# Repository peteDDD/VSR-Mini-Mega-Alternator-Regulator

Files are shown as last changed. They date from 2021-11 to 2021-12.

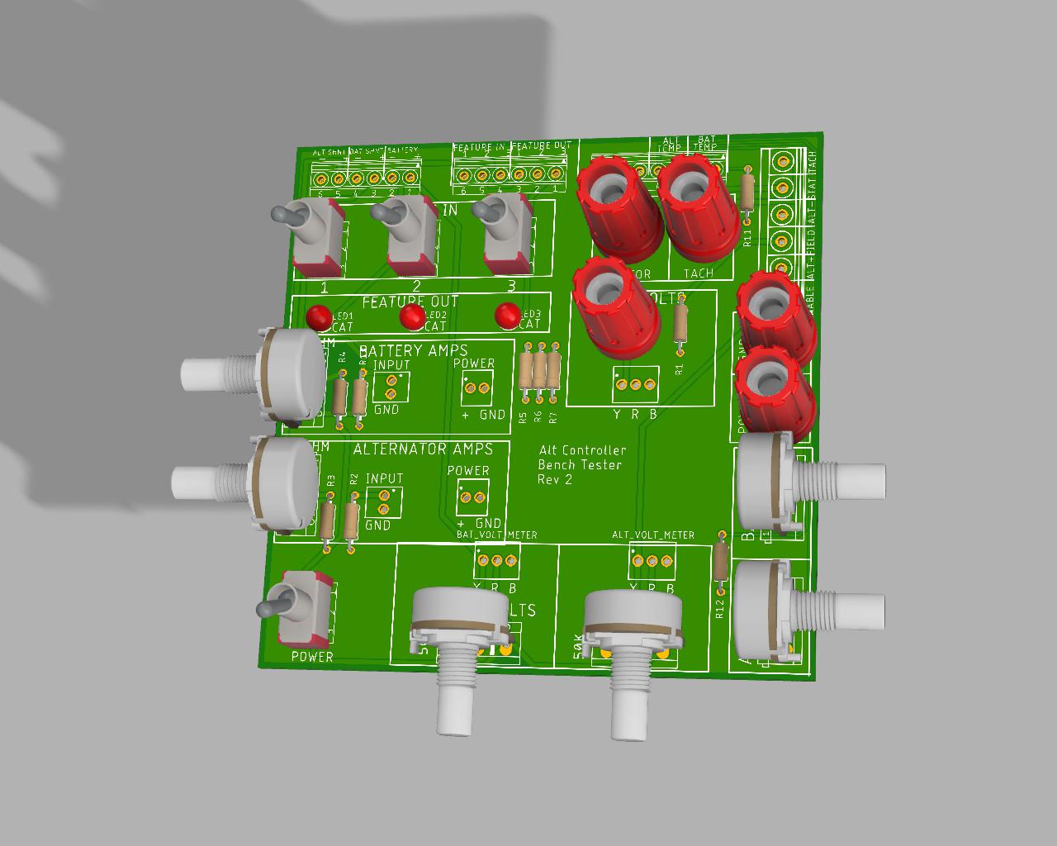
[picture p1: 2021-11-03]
Documentation/Bench Tester 0.2.jpg

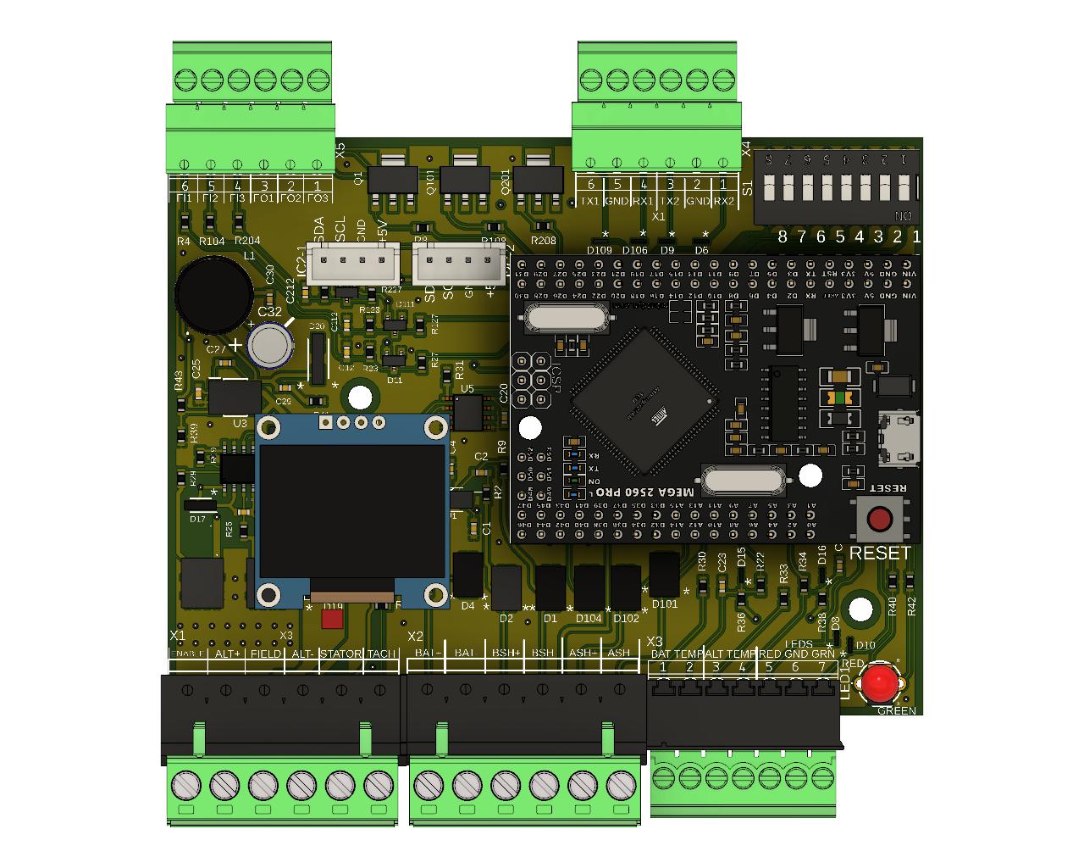
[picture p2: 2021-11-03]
Documentation/VSR Mini Mega with Connectors and oled v5.jpg

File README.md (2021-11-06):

# VSR-Mini-Mega-Rev-1

This project is a refactoring of the amazing work of William A. Thomason ("Al") to create an open source very smart alternator regulator.  That work can be seen here:
http://arduinoalternatorregulator.blogspot.com/

That open-source hardware is no longer orderable through Al.  In January 2019, that product "went pro" and is now available as a commercial product as you can see here:
http://wakespeed.com/products.html

In December 2020 I began refactoring Al's code to remove CAN and Bluetooth related code and move the hardware to a new PC board with a Mini Mega Pro 2560 daughter card
as the processor. Thus "VSR MINI MEGA" was born.

I wanted to remove some functionality and add other functionality.  Also, moving to the Mini Mega Pro 2560 provided more memory for expansion.

New hardware features include:
  - Dual INA226 current voltage sensors (for Alternator and Battery)    * Al's designs supported a second shunt but required a separate battery monitor to implement 
      that very unique and powerful functionality.  THe VSR MINI MEGA directly support two shunts.
  - Three Feature-in Ports and Three Feature-out Ports (functionality and port assignments selectable in Config.h)  
  - Two serial port screw headers, separate from port used to USB programming, one can support external full function display 
       (A remote display based on an Arduino Uno and a TFT color display will be published in the near future)
  - Two I2C pin headers to add an in-case OLED display or other features
  - Red and green LED output connections (independent of the Feature-out option which preceeded it).  
 
New firmware features include, selectable and configurable in Config.h include  :  
  - ENABLE_FEATURE_IN_SCUBA  - uses one of the Feature-in ports to shift the alternator field PWM way down so a small engine can run a SCUBA compressor while maintaining a 
      bit of output for keeping up with an electric clutch and relays used by the SCUBA compressor.
 -  FEATURE_OUT_GREEN_LED, FEATURE_OUT_RED_LED - echo the red and green status LED to your choice of Feature-out ports.
 -  FEATURE_OUT_LIFEPO_SHUTDOWN_ALARM - provides a Feature-out alarm which follows the Force-o-Float Feature-in
 -  USE_OLED - provides a class-based OLED display which displays realtime alternator and battery voltage, current, and temperatures, field PWM, current charging mode, 
      time in that mode, flags like "Forced Float" and "SCUBA", and error messages.  The display also reflects the DIP switch settings in human-speak at boot up.
 -  USE_SERIAL_DISPLAY - supports Arduio Uno-based color TFT display which alternately displays a screen showing alternator amps and battery voltage and a graphical display
      of the actual charging curve (amps and volts) over time
      
Features and firmware removed include (as best I can so far)
 -  CAN support
 -  Bluetooth artifacts from earlier VSR versions
 -  Engine control artifacts from Al's 6HP 12V diesel genset/water maker which preceded the VSR alternator regulator.
 -  Remote battery monitor artifacts
 
Future (near-term) enhancements planned:
 -  There is a stub in this release to support monitoring LiFePO4 battery management system's output for a pending battery disconnect.  This will then trigger a "Force-to-float"
      on the Mini-Mega to protect the alternator from a battery disconnect.
      
Also developed:
 -  Bench testing board to mimic battery and alternator voltages, currents, and temperatures, and feature-in and feature-out functions (switches and LEDs respectively)  
      This board also can have small volt and current meters on it and bannana jacks for stator input (from a signal generator) and tach out (to a frequency counter or 
      oscilloscope.
 -  The previously-mentioned remote color graphical display
 -  3D-printed case for VSR Mega-Mini with 0.93" OLED
 -  3D-printed bezel for the remote color graphical display

 FULL REFERENCE MANUAL CAN BE FOUND IN THE DOCUMENTATION DIRECTORY.
 
 ###

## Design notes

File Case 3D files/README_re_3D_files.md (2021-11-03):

Regarding the case lids and the OLED snap-in mount, I have found that there is some variance in the dimensions of the OLED boards.
To accomodate this, I made the snap clips a bit bigger than might be necessary.  Carefully trim *two* of the clips (I like to trim
the ones closest to the side of the case) slightly with a razor blad to adjust the degree of pressure needed to press your OLED board 
into position.

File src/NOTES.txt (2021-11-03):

started with SmartRegulatorv1.3.1.2020_12StableE_for_10b

1) DONE --  I2c.write(INA226_EXTERNAL_I2C_ADDR, CONFIG_REG, ptr, 2);  

  //DUBLER 061720    adding external INA226
  #ifdef USE_EXTERNAL_INA226
  i2c_start(INA226_EXTERNAL_I2C_ADDR << 1 | I2C_WRITE);
  i2c_write(CONFIG_REG); // Writing the Config reg also 'triggers' a INA226 sample cycle.
  i2c_write(highByte(INA226_CONFIG));// MSB always goes 1st
  i2c_write( lowByte(INA226_CONFIG));
  i2c_stop();

2) DONE -- cpu is AVR  eliminateed #ifdef AVR

3) DONE -- Change INA226 to INA226-bat  and external_INA226 to INA226-alt

4) DONE -- Scrub smartregulator.h to configure to ATmega2560 MINI PRO EMBED

5) DONE -- do we need CHARGE_PUMP_PORT (likely just for bluetooth)
   system.cpp line 424

6) DONE -- what is RVCMessages.h  used in system.h  ... NMEA2000 stuff
   GET RID OF N2K stuff

7) DONE -- research WDT on ATmega2650

8) DONE -- systemVoltMult in main code.   decide if we need this or not.

9) DONE --decide what functions we want to map to the dip switch.   Set this up in the main code.
   Perhaps add label on board for DIP switch functions  Add tach mode and engine stop function (activate feature_out_3 pulse after X time in float mode)

10) DONE -- review DIP switch code.  May be able to ifdef in simpler code since pins are now assigned to a single port.

11) DONE -- Look into #ifdef NTC_FET_PORT (not turned on yet... Pin 7 of Mega board)

12) DONE -- Change feature_out_port to support multiple feature out ports -- continue to complete... now has 
      feature in/out port defines.

13) DONE -- Move serial port for serial display out to a different serial port.  Reserve primary serial port for
    programming and configuring.  CONFIGURE MULTIPLE SERIAL STREAMS

14) On 3D printed case, engrave terminal names.

15) DONE -- have we eliminated all references to AVR and OSE_ALTERNATOR defines?

16/ DONE -- NOTE BOM R1 and R101 are now 10 ohm

17) DONE --Need to implement a failsafe for lithium batteries in the combiner funtion.

18) Confirm that Lifeline profile agrees with Lifeline specs.

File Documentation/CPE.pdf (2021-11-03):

const tCPS PROGMEM defaultCPS[MAX_CPES] = {

// eliminated decimal places to fix conversion narrowing problem. Note that, for example, 6 hours uses 60 here and 4.5 hours uses 45 | Min | Bat | Bat
// Name | BULK/ACCEPTANCE | Min | Temp Min | Max
Target | | | Limit Exit | Exit | Limit | Exit | | | | Equal Limit | Exit | Exit | Temp | Temp Chrg Chrg
Volts | Duration | Amps | Amps Volts | Duration | Volts Amps | Duration | Amps Ahrs Volts | Duration | Volts Ahrs | Volts Amps | Duration | Amps | Comp | Limit Temp Temp
{"LIFELINE" | 14.3 | 60 * 360000UL 15 | 0 | 0 | 0 * 360000UL | 13.3 | -1 | 0 * 360000UL | -10 | 0 | 12.8 | 0 * 360000UL | 0 | 0 | 0 | 0 | 0 * 360000UL | 0 | 0.0234 | -9 | -45 | 45} // LIFELINE BATTERY #1 Default (safe) profile & AGM #1 (Low Voltage AGM).
{"STD FLA" | 14.8 | 30 * 360000UL | 5 | 0 | 0 | 0 * 360000UL | 13.5 | -1 | 0 * 360000UL | -10 | 0 | 12.8 | 0 * 360000UL | 0 | 0 | 0 | 0 | 0 * 360000UL | 0 | 0.005 * 6 | -9 | -45 | 45} // #2 Standard FLA (e.g. Starter Battery small storage)
{"HD FLA" | 14.6 | 45 * 360000UL | 5 | 0 | 0 | 0 * 360000UL | 13.2 | -1 | 0 * 360000UL | -10 | 0 | 12.8 | 0 * 360000UL | 0 | 0 | 15.3 | 25 | 30 * 360000UL | 0 | 0.005 * 6 | -9 | -45 | 45} // #3 HD FLA (GC, L16, larger)
{"AGM #2" | 14.7 | 45 * 360000UL | 3 | 0 | 0 | 0 * 360000UL | 13.4 | -1 | 0 * 360000UL | -10 | 0 | 12.8 | 0 * 360000UL | 0 | 0 | 0 | 0 | 0 * 360000UL | 0 | 0.004 * 6 | -9 | -45 | 45} // #4 AGM #2 (Higher Voltage AGM)
{"GEL" | 14.1 | 60 * 360000UL | 5 | 0 | 0 | 0 * 360000UL | 13.5 | -1 | 0 * 360000UL | -10 | 0 | 12.8 | 0 * 360000UL | 0 | 0 | 0 | 0 | 0 * 360000UL | 0 | 0.005 * 6 | -9 | -45 | 45} // #5 GEL
{"FIREFLY" | 14.4 | 60 * 360000UL | 7 | 0 | 0 | 0 * 360000UL | 13.4 | -1 | 0 * 360000UL | -20 | 0 | 12.0 | 0 * 360000UL | 0 | 0 | 14.4 | 0 | 30 * 360000UL | 3 | 0.024 | -20 | -20 | 50} // #6 Firefly (Carbon Foam)
{"CUSTOM " | 14.4 | 60 * 360000UL 15 | 15 | 5.3 30 * 360000UL | 13.1 | -1 | 0 * 360000UL | -10 | 0 | 12.8 | 0 * 360000UL | 0 | 0 | 15.3 | 25 | 30 * 360000UL | 0 | 0.005 * 6 | -9 | -45 | 45} // #7 4-stage HD FLA (& Custom #1 changeable profile)
{"LiFePO4 " | 13.8 | 10 * 360000UL 15 | 0 | 0 | 0 * 360000UL | 13.6 | 0 | 0 * 360000UL | 0 | -50 13.3 | 0 * 360000UL | 0 | 0 | 0 | 0 | 0 * 360000UL | 0 | 0.000 * 6 | 0 | 0 | 40} // #8 LiFeP04 | (& Custom #2 changeable profile

Exit Accpt

FLOAT | POST-FLOAT TO BULK | EQUALIZATION

FLOAT TO BULK

OVERCHARGE

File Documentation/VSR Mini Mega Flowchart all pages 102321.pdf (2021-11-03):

# VSR Mini Mega Firmware Flow Chart (page 1 of 3)

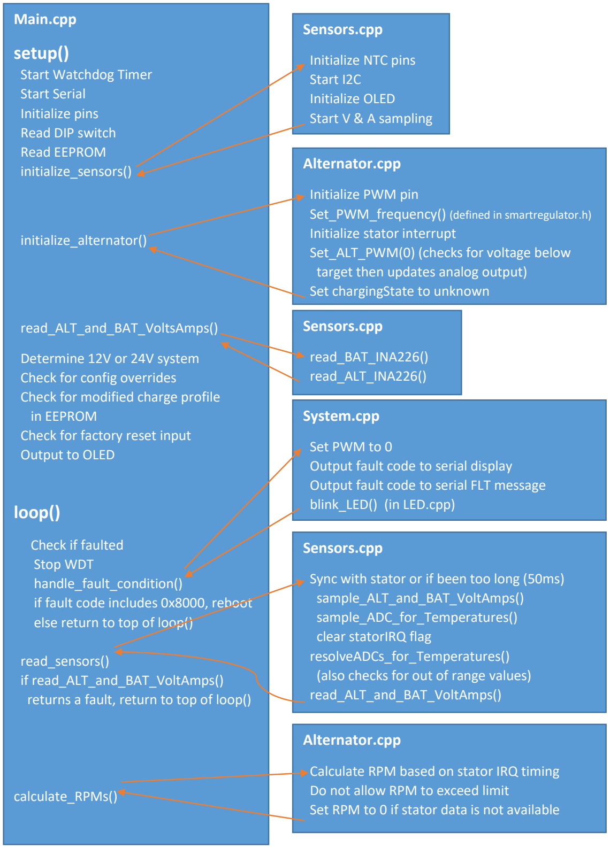
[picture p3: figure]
Main.cpp; setup(); Start Watchdog Timer Start Serial Initialize pins Read DIP switch Read EEPROM initialize_sensors(); initialize_alternator(); read_ALT_and_BAT_VoltsAmps(); Determine 12V or 24V system Check for config overrides Check for modified charge profile in EEPROM Check for factory reset input Output to OLED; loop(); Check if faulted Stop WDT handle_fault_condition() if fault code includes 0x8000, reboot else return to top of loop(); read_sensors() if read_ALT_and_BAT_VoltAmps(); calculate_RPMs(); Sensors.cpp; Initialize NTC pins Start I2C Initialize OLED Start V & A sampling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

returns a fault, return to top of loop()

Sync with stator or if been too long (50ms)

Calculate RPM based on stator IRQ timing

Set RPM to 0 if stator data is not available

# VSR Mini Mega Firmware Flow Chart (page 2 of 3)

Main.cpp (continued from page 1)

Calculate_ALT_targets()

Check for faults,
if any, return to top of loop()

manage_ALT()

manage_system_state()
if chargingState is unknown or disabled, transition to warm-up

handle_feature_in()

(Continued on page 3)

Alternator.cpp

Validate cpIndex – if invalid, fault
if measuredBatTemp is out of range,
set chargemode to float_charge switch(chargingState) to find BAT_V_SETPOINT, targetAltAmps, and targetAltWatts based on current chargingState. Calls set_VAWL()

Set_VAWL()
sets targetBatVolts, scaled to systems voltage if alt temp sensor shorted, targetAltAmps are set to ALT_AMP_DERATE_HALF_POWER elseif smallAltMode, scale targetAltAmps and fieldPWMLimit by
ALT_AMP_DERATE_SMALL_MODE
else scale by ALT_AMP_DERATE_NORMAL

if RPMs != 0, protect slow spinning alternator

if chargingState == determine_Alt_CAP, set values way high
else set targetALtWatts to ALT_WATT_LIMIT

Alternator.cpp

if updatingBatVAs or updatingAltVAs, return if not time to update PWM, return
Conduct PID magic to adjust fieldPWM Switch(chargingState) to manage transitions between charging states
Check for fieldPWM limits
set_ALT_PWM()
if sendDebugString == true,
build and write debug string and set SDMCounter to SDM_SENSITIVITY

System.cpp

Scan and handle feature-in pins

# VSR Mini Mega Firmware Flow Chart (page 3 of 3)

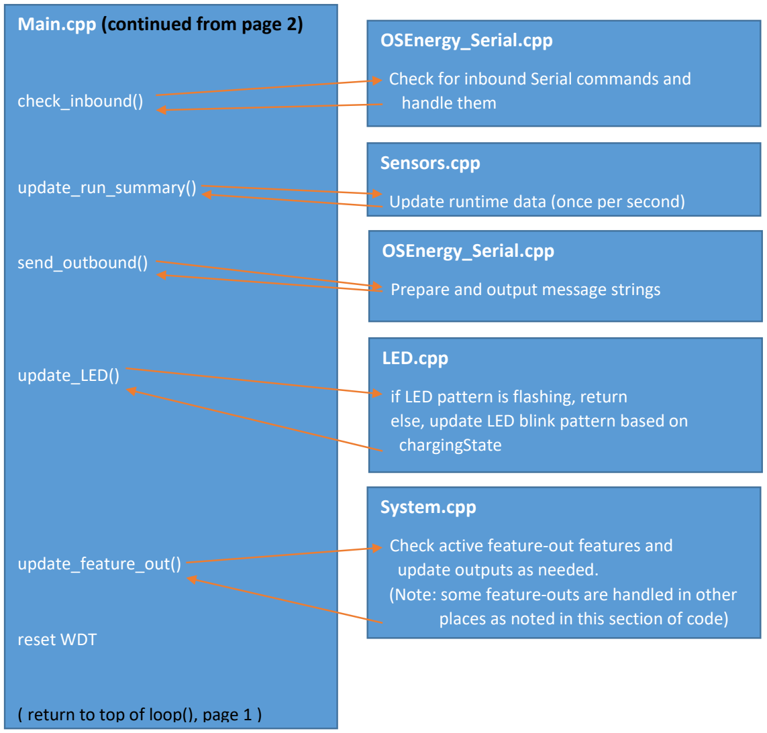
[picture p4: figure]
Main.cpp (continued from page 2); check_inbound(); update_run_summary(); send_outbound(); update_LED(); update_feature_out(); reset WDT; ( return to top of loop(), page 1 ); OSEnergy_Serial.cpp; Check for inbound Serial commands and handle them; System.cpp; Check active feature-out features and update outputs as needed.; Sensors.cpp; Update runtime data (once per second); Prepare and output message strings; LED.cpp; if LED pattern is flashing, return else, update LED blink pattern based on chargingState

(Note: some feature-outs are handled in other places as noted in this section of code)

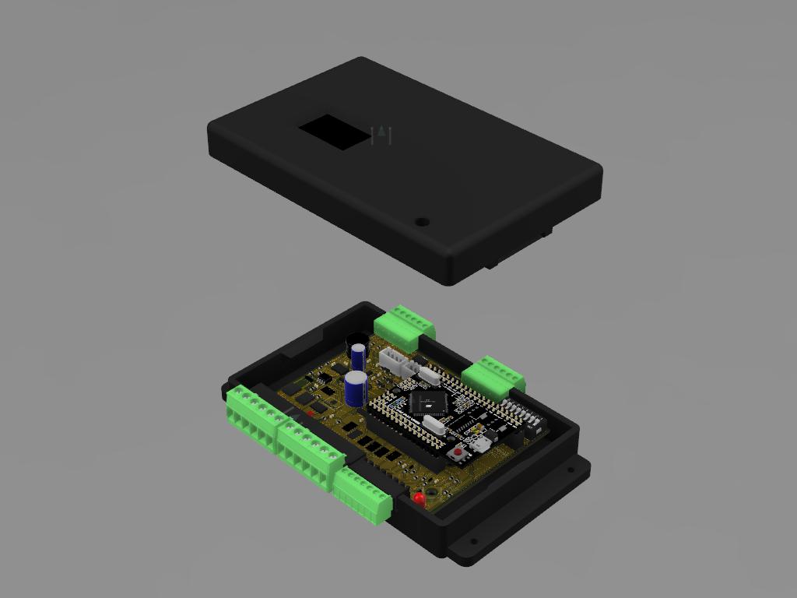
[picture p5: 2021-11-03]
Documentation/VSR Mini Mega Universal Snap Lid Box.jpg

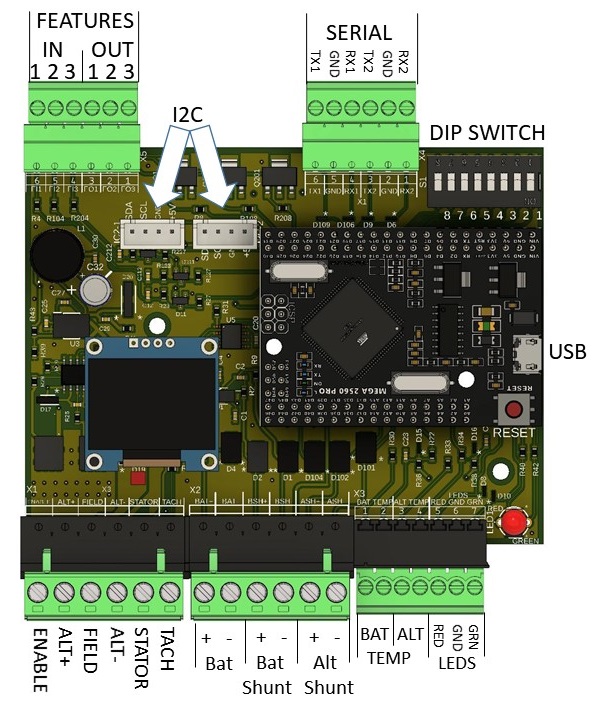
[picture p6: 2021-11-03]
Documentation/VMMAR Connections.JPG

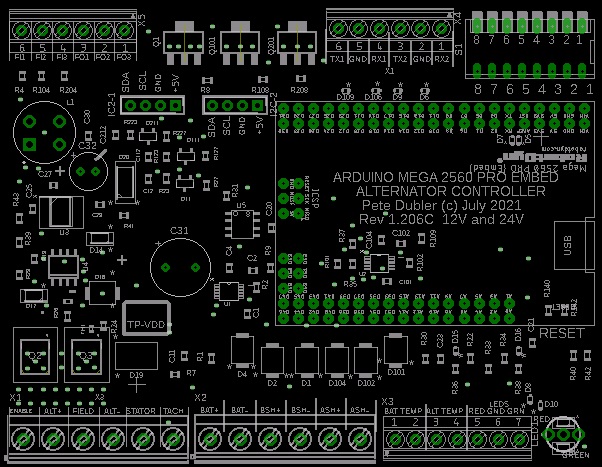
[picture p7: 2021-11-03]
Documentation/VSR Mini Mega PCB Image 2D.jpg

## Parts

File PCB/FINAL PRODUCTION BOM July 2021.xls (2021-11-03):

PCBWay Bom Quotation , Product No.:T-Y7W387690A
Item # | *Designator | *Qty | Manufacturer | *Mfg Part # | Description / Value | Vendor Part # | *Package/Footprint | *Unit Price(4 sets) | *Total | *Delivery Time | *Actual Purchase Mfg Part # | *PCBWay Note
1 | C11,C29 | 2 |  |  | 150pF『 』25V 10%『 』C-EUC0603『 』CAPACITOR, European symbol |  | C0603 | $0.037 | $0.296 |  | CC0603KRX7R9BB151
2 | C1,C2,C4,C12,C20,C25,C27,C101,C102,C104,C112,C212 | 12 | Yageo | CC0603KRX7R8BB104 | 0.1uF『 』25V 10%『 』C-EUC0603『 』CAPACITOR, European symbol | 603-CC603KRX7R8BB104 | C0603 | $0.011 | $0.528
3 | C21,C23,C30 | 3 | Taiyo Yuden | TMK107BJ474KA-T | 0.47uF『 』25V 10%『 』C-EUC0603『 』CAPACITOR, European symbol | 963-TMK107BJ474KA-T | C0603 | $0.141 | $1.692
4 | C18 | 1 | Taiyo Yuden | TMK107BBJ475KA-T | 4.7uF『 』25V X7R 10%『 』C-EUC0603K『 』CAPACITOR, European symbol | 963-TMK107BBJ475KA-T | C0603K | $0.198 | $0.792
5 | C31 | 1 | Nichicon | UHE2A470MPD | 47uF/100V『 』『 』CPOL-USTT5D10『 』POLARIZED CAPACITOR, American symbol | 647-UHE2A470MPD | TT5D10 | $0.181 | $0.724
6 | C32 | 1 | Nichicon | UHD1V560MED | 56uF/35V『 』『 』CPOL-USE2.5-7『 』POLARIZED CAPACITOR, American symbol | 647-UHD1V560MEDAlternates:667-EEU-FC1V560B647-UPV1V560MGD667-EEU-FC1V560647-UPM1V560MED1TD | E2,5-7 | $0.694 | $2.776 | 7-10 work days | EEU-FC1V560B
7 | R1,R2,R9,R26,R29,R101,R102,R109 | 8 |  |  | 10 ohm『 』1% or better『 』R-EU_R0603『 』RESISTOR, European symbol |  | R0603 | $0.008 | $0.256 |  | RC0603FR-0710RL
8 | R22,R27,R30,R33,R34,R41,R127,R227 | 8 |  |  | 100 ohm『 』1% or better『 』R-EU_R0603『 』RESISTOR, European symbol |  | R0603 | $0.006 | $0.192 |  | RC0603FR-07100RL
9 | R8,R19,R40,R42,R108,R140,R142,R208 | 8 |  |  | 1K『 』1% or better『 』R-EU_R0603『 』RESISTOR, European symbol |  | R0603 | $0.006 | $0.192 |  | RC0603FR-071KL
10 | R24,R35,R36,R37,R38 | 5 |  |  | 10K ohm『 』1% or better『 』R-EU_R0603『 』RESISTOR, European symbol |  | R0603 | $0.008 | $0.160 |  | RC0603FR-0710KL
11 | TH1 | 1 | Murata | NCP15XH103F03RC | 10K NTC『 』1% or better『 』R-EU_R0402『 』RESISTOR, European symbol | 81-NCP15XH103F03RC | R0402 | $0.452 | $1.808
12 | R4,R7,R31,R104,R204 | 5 |  |  | 37.4K ohm『 』1% or better『 』R-EU_R0603『 』RESISTOR, European symbol |  | R0603 | $0.008 | $0.160 |  | RC0603FR-0737K4L
13 | R39 | 1 |  |  | 100K ohm『 』1% or better『 』R-EU_R0603『 』RESISTOR, European symbol |  | R0603 | $0.041 | $0.164 |  | RC0603FR-07100KL
14 | R23,R43,R123,R223 | 4 |  |  | 1M ohm『 』1% or better『 』R-EU_R0603『 』RESISTOR, European symbol |  | R0603 | $0.011 | $0.176 |  | RC0603FR-071ML
15 | L1 | 1 | Murata | 12LRS684C | 12LRS684C『 』『 』12LRS684C『 』 | 580-12LRS684C | IND_12LRS156C | $0.981 | $3.924 | 7-10 work days
16 | D11,D111,D211 | 3 | ON Semiconductor | BAT54SLT1G | BAT54S『 』『 』BAT54S『 』Schottky Diodes | 863-BAT54SLT1G | SOT23 | $0.245 | $2.940
17 | D5,D6,D7,D8,D9,D10,D15,D16,D106,D109 | 10 | ON Semiconductor | ESD5Z5.0T1G | ESD5Z5.0T1G『 』『 』ESD5Z5.0T1G『 』 | 863-ESD5Z5.0T1G | SOD523 | $0.121 | $4.840
18 | D19 | 1 | ON Semiconductor | FSV20100V | FSV20100V『 』『 』FSV20100V『 』Diode Schottky 100V 20A Surface Mount TO-277-3 Good Diode Schottky 100V 20A Surface Mount TO-277-3 ON Semico | 512-FSV20100V | TO-277 | $1.875 | $7.500 | 7-10 work days | FSV20120V | We will supply FSV20120V
19 | D14,D17 | 2 | ON Semiconductor | S110FA | S110FA『 』『 』S110FA『 』Schottky Diodes & Rectifiers 100V 1A Schottky Barrier Rectifier Schottky Diodes & Rectifiers 100V 1A Schottky Barrier Rectifier 1.43mm ON Semiconductor S110FA | 512-S110FA | SODFL3618X143N | $0.641 | $5.128 | 7-10 work days
20 | D1,D2,D4,D101,D102,D104 | 6 | STMicroelectronics | SMAJ30A-TR | SMAJ30A『 』『 』SUPPRESSOR-SMBJ『 』Suppressor diode | 511-SMAJ30A-TR | SMBJ | $0.136 | $3.264
21 | D18 | 1 | Vishay | SMAJ64A-E3 | SMAJ64A『 』『 』SUPPRESSOR-SMBJ『 』Suppressor diode | 625-SMAJ64A-E3 | SMBJ | $0.525 | $2.100 | 7-10 work days | SMAJ60A | Brand:Bourns
22 | D20 | 1 | Vishay | SMAJ64A-E3 | SSA210『 』『 』SSA210『 』Diode Schottky 100V 2A 2-Pin SMA T/R Diode Schottky 100V 2A 2-Pin SMA T/R 2.7mm ON Semiconductor SSA210 | 625-SMAJ64A-E3 | DIOM5227X270N | $0.624 | $2.496 | 7-10 work days | VSSA210-M3/61T
23 | LED1 | 1 | Kingbright | WP59EGW | WP59EGW『 』『 』WP59EGW『 』5MM BI-COLOR RED/GRN LED LAMP THRU-HOLE Kingbright WP59EGW | 604-WP59EGWor similar | T-1_3/4(5MM)_BI-COLOR_LED | $0.788 | $3.152 | 7-10 work days
24 | U1,U2 | 2 | TI | INA226AIDGSR | INA226『 』『 』INA226『 』CURRENT/POWER MONITOR with Two-Wire Interface | 595-INA226AIDGSR | SOP50P490X110-10N | $2.858 | $22.864
25 | U3 | 1 | Maxim Integrated | MAX5033DASA+ | MAX5033DASA+『 』『 』MAX5033DASA+『 』DC-DC Converter Step Down 7.5V to 76V DC-DC Converter Step Down 7.5V to 76V 1.75mm Maxim Integrated MAX5033DASA+ | 700-MAX5033DASA | SOIC127P600X175-8N | $3.100 | $12.400
26 | U4 | 1 | Microchip | MIC4604YM-TR | MIC4604SOIC-8『 』『 』MIC4604SOIC-8『 』 | 998-MIC4604YM-TR | SOIC8 | $1.042 | $4.168 | 7-10 work days
27 | U5 | 1 | ON Semiconductor | NCV1124DR2G | NCV1124SO-8『 』『 』NCV11124SO-8『 』 | 863-NCV1124DR2G | SO-8 | $3.315 | $13.260
28 | Q1,Q101,Q201 | 3 | ON Semiconductor | NZT605 | NZT605SOT223『 』『 』NZT605SOT223『 』NPN Darlington Transistor | 512-NZT605 | SOT223 | $0.478 | $5.736 | 7-10 work days
29 | Q2,Q3 | 2 | Diodes Inc | DMTH6005LPSQ-13 | DMTH6005LPSQ-13『 』『 』TPW4R50ANH『 』 | 621-DMTH6005LPSQ-13 | TRANS_STL60P4LLF6 | $3.986 | $31.888 | 7-10 work days
30 | X1,X5 | 2 |  | 1751280 | 6p 3.5mm RIGHT-ANGLE male and female header made in China Picture below |  |  | $0.400 | $3.200 |  |  | we will provide 6p 3.5mm RIGHT-ANGLE male and female header made in China,pls confirm photos.
31 | X2 | 1 |  | 1751293 | 7p 3.5mm RIGHT-ANGLE male and female header made in China,pls confirm photos. Picture below | 651-1751293 |  | $0.500 | $2.000 |  |  | we will provide 7p 3.5mm RIGHT-ANGLE male and female header made in China,pls confirm photos.
32 | X3,X4 | 2 |  | 1729160 | 6p 5.08mm RIGHT-ANGLE male and female header made in China,pls confirm photos. Picture below | 651-1729160 |  | $0.250 | $2.000 |  |  | we will provide 6p 5.08mm RIGHT-ANGLE male and female header made in China,pls confirm photos.
33 | I2C-2,IC2-1 | 2 | Wurth Elektronik | 61300411021 - Gold-Plated | 61300411121『 』『 』61300411121『 』WR-PHD 2.54mm Pin Header THT Straight 4p Wurth Elektronik | B-2100S04P-A110 |  | $0.210 | $1.680 |  | XH2.54 4Pin Pitch 2.54mm | We will supply XH2.54 4Pin Pitch 2.54mm，pls confirm photo
34 | S1 | 1 | CTS Electronic Components | 2108MS | DP08『 』『 』DP08『 』DIL/CODE SWITCH 8-switches | 210-8MS | DP-08 | $1.130 | $4.520 |  | 210-8MS
35 |  | 2 |  | 2*3PIN 2.54MM FEMALE HEADER - Gold-Plated | see illustration and eBay number below |  |  | $0.000 | $0.000 |  |  | Provided by customer
36 |  | 1 |  | 2*16PIN 2.54MM FEMALE HEADER - Gold-Plated | see illustration and eBay number below |  |  | $0.000 | $0.000 |  |  | Provided by customer
37 |  | 4 |  | 2*21PIN 2.54MM FEMALE HEADER - Gold-Plated | see illustration and eBay number below. |  |  | $0.000 | $0.000 |  |  | Provided by customer
 |  |  |  |  |  |  |  | All Total | $148.976
38 | PROCESSOR | 1 | AliExpress |  | MEGA 2560 PRO Embed CH340G/ATMEGA2560-16AU Chip with male pinheaders | https://www.aliexpress.com/item/1005001621855512.html |  |  |  |  |  | Provided and installed by customer
39 | OLED | 1 | AliExpress |  | 10PCS 0.96 inch IIC Serial White OLED Display Module 128X64 I2C SSD1306 12864 LCD Screen Board GND VCC SCL SDA 0.96" for arduino | https://www.aliexpress.com/item/1005001484061311.html |  |  |  |  |  | Provided and installed by customer
40 | OLED cable | 1 | AliExpress |  | JST XH2.54 XH 2.54mm Wire Cable Connector 2/3/4/5/6/7/8/9/10/11/12/13 Pin Pitch Male Female Plug Socket 30cm Wire Length 26AWG | https://www.aliexpress.com/item/32911598577.html |  |  |  |  |  | Provided and installed by customer
 | 2x16 |  |  |  | 2x3 | 2x21
eBay | 171074645303 |  |  |  | 181112092760 | 183425891144

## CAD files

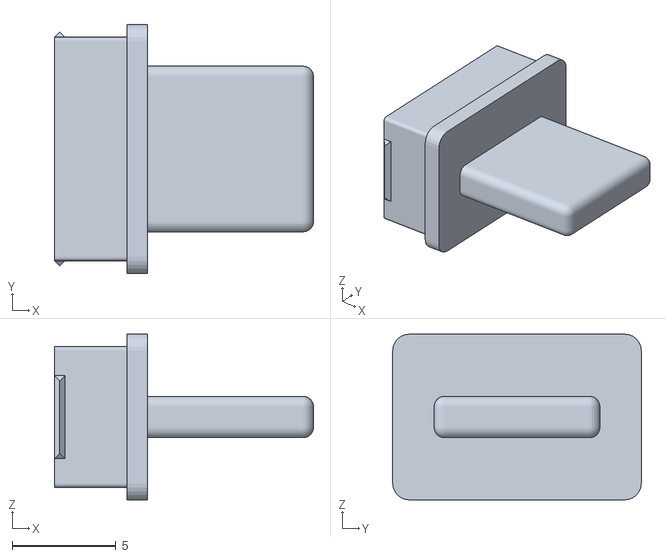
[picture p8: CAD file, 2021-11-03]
Case 3D files/VSR Mini Mega CaseUSB Hole Plug.stl
12.5 x 12.0 x 8.00

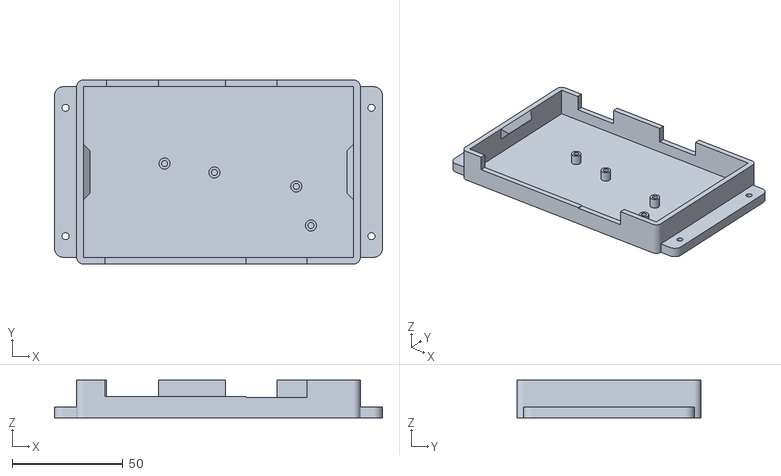
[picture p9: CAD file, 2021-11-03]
Case 3D files/VSR Mini Mega Case Bottom.stl
148.0 x 83.0 x 17.0

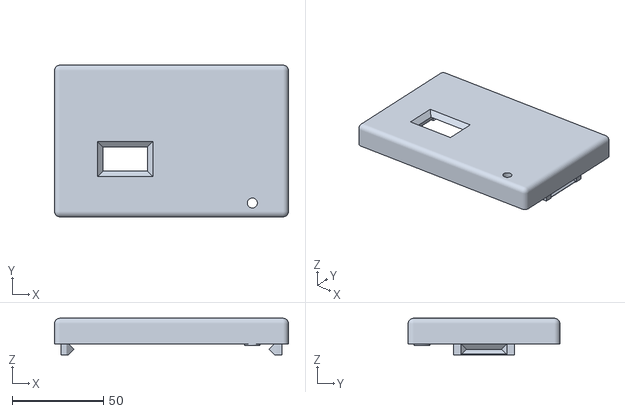
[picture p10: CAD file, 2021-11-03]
Case 3D files/VSR Mini Mega Case Snap Lid without USB hole.stl
128.0 x 83.0 x 20.0

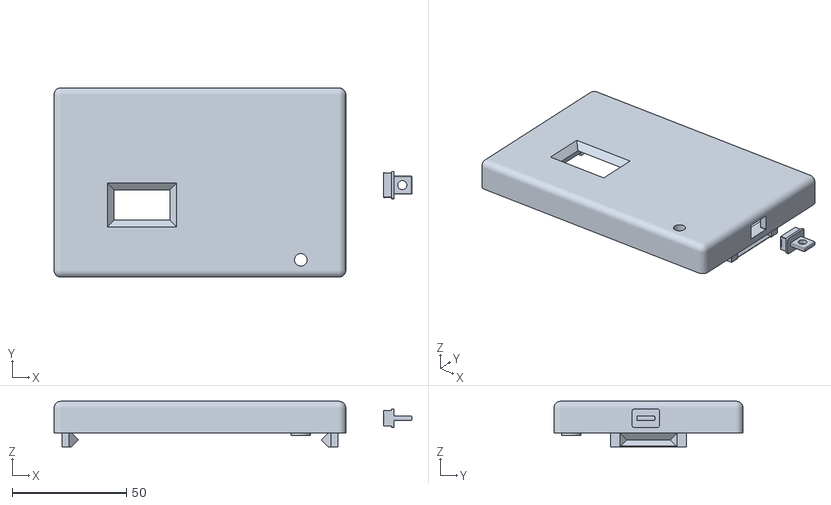
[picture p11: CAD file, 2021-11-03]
Case 3D files/VSR Mini Mega Case Snap Lid with USB hole.stl
157.0 x 83.0 x 20.0

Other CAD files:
Case 3D files/VSR Mini Mega Case USB Hole Plug with round hole.stl

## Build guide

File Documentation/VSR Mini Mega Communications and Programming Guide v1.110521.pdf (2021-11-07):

# VSR Mini Mega Alternator Regulator

# Communications and Programming Guide

Copyright 2018 – William A. Thomason

Refactored Copyright 2021 – Pete Dubler

Released Under Creative Commons Attribution-Noncommercial-Share Alike 3.0 http://creativecommons.org/licenses/by-nc-sa/3.0/

V1.110621

## Table of Contents

## ABOUT THIS GUIDE

The guide is based on the guide for the VSR series of product offerings developed (or contemplated) by William A. (“Al”) Thomason. The suite of communications features has be reduced to align with the features of the VSR Mini Mega Alternator Regulator (VSMMAR) and does not apply to any other devices, current or contemplated.

This guide is documents communications into and out of the VSMMAR on the serial USB port and messages which may be sent out of one of the other two serial ports (Serial1 and Serial2) which may be configured to support the Remote TFT Display feature.

You will soon see that setting parameters using serial commands is very powerful, but quite tedious. Using the Dashboard tool (once it becomes available for the VSMMAR) gives you all this power without the tedium. Nonetheless, refer to this guide to understand the parameters in detail.

## ASCII COMMUNICATIONS

The Mini Mega processor daughter card of the VSMMAR features a built in micro-USB port to allow for advanced monitoring, diagnostics, configuration, and firmware updates. Simply connect a USB cable (making sure it is a proper data USB cable, and not a charger-only cable) between your computer and the USB micro port and utilize a terminal in Visual Studio Code/PlatformIO, the monitor in the Arduino IDE, or a serial terminal app such as Putty (see below).

### TERMINAL PROGRAMS

Many operating systems have built-in terminal programs, as does the Arduino IDE. After connecting the regulator to the computer you can use one of these to open a communications window to the VSMMAR.

NOTE: Some terminal programs do not send a complete end-of-line terminator (CR+LF - specifically, Arduino’s Serial Monitor). To support these environments, the VSMMAR will recognize the character ‘@’ as an alternative EOL.

Remember that any configuration changes you make to the regulator via ASCII commands may not take effect until the regulator is rebooted. When you have finished making changes, make sure to issue the $RBT: command to not only assure changes are saved to the regulators’ non-volatile memory, but that the changes are then utilized by the regulator. (Refer to $RBT: - ReBooT system on page 32) After rebooting the VSMMAR verify the changes you sent were indeed recognized by the regulator by inspecting the various status strings.

PuTTY: Another versatile option is the free ‘PuTTY’ program (www.putty.org ). It supports a wide range of operating systems and includes a very nice logging function. To use, connect up the USB cable to the PC and start Putty. Configure as shown here – selecting the Serial COM port which your USB serial port is associated with, and setting the speed to 9600 and clicking the Connection Type: Serial button.

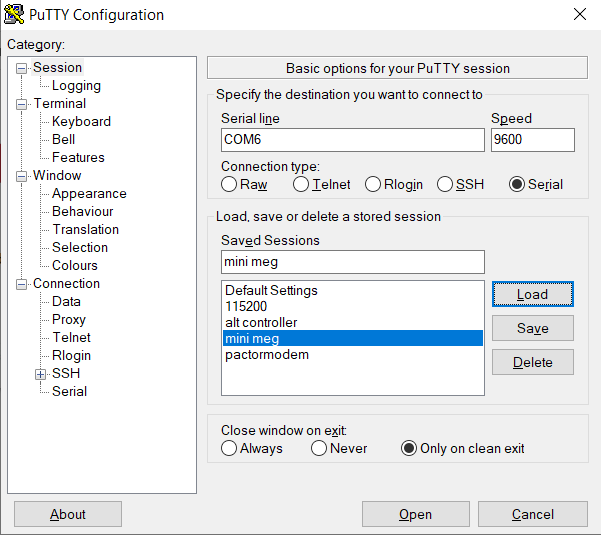
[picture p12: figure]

Next click on the ”Terminal” in the Category tree on the left side of the PuTTY window and duplicate the settings shown here:

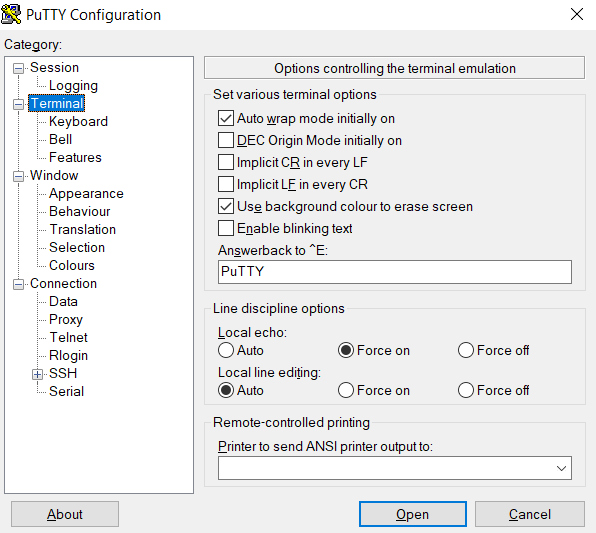
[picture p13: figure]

If you wish to keep a log file of the session, click on “Logging”, under ”Session”, in the Category tree on the left side of the PuTTY window, enter a file name and mimic the settings shown here:

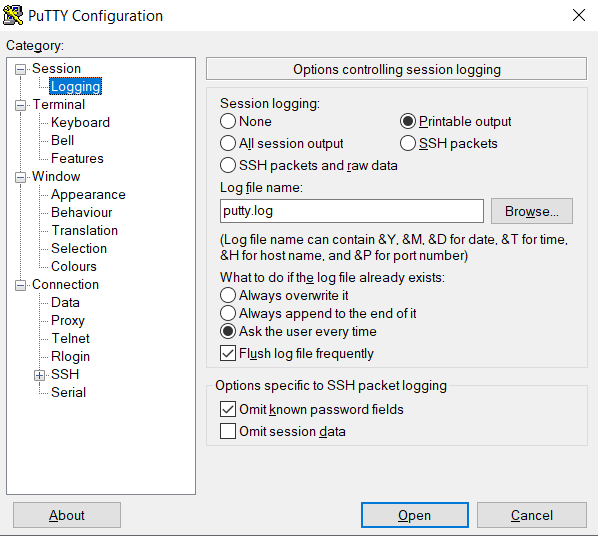
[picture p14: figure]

Logging sessions is very helpful for debugging your installations, the files are comma separated and easily import into Excel using the import wizard specifying commas (,) as the separator. Refer to Appendix A: Receiving data FROM the VSMMAR: for details on the output.

Finally, after making all these settings, consider returning to the “Session” item in the Category tree and saving the PuTTY configurations for later by typing a new name in the “Saved Sessions” space and then clicking “Save”. The new session name will appear in the list of saved sessions. Next time you open Putty, you can click on the name of that saved session and then click “Load” to reload all of the setting.

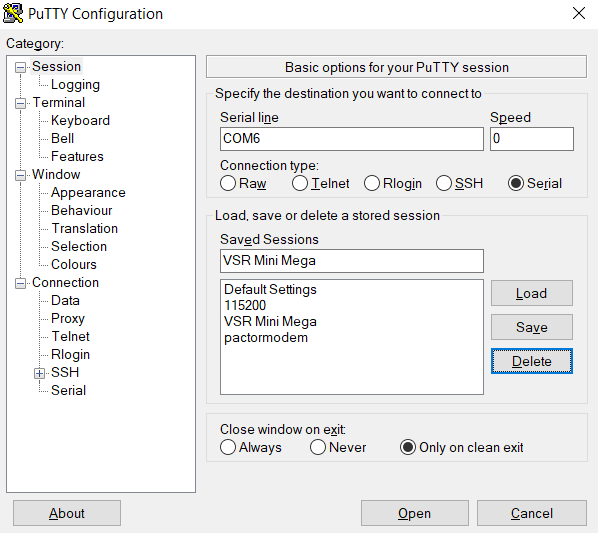
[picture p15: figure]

Once you have completed the configuration, or when you reload the settings, click the “Open” button to start the terminal session.

Bench-top Configuration: When a USB cable is connected to the VSMMAR and PC, power is supplied to the logic portion of the hardware. This allows you to do bench-top configuration before completing the installation and connecting the actual alternator, battery, shunts, etc.

Again… remember to be sure to send a $RBT: command as your last step, to assure changes are recorded. (And add an “@” to the end of each command line if needed to get the VSMMAR to respond to the commands). After the regulator reboots make sure to verify your changes before installing the regulator in a live installation.

### OVERVIEW OF ASCII COMMUNICATIONS WITH THE VSMMAR

- The VSMMAR outputs status strings on a continuous basis.
- The automatically output status strings are divided into two categories: major and minor
- The minor strings are output once for every ten times the major strings are output. So, for example, ten $AST strings will be followed by one $SST string.
- ASCII message strings can be sent to the VSMMAR to either
a. request a particular message string be output by the VSMMAR (for example: $CPE:0 asks the VSMMAR to return the current CPE settings), or
b. set parameters of the VSMMAR by sending the appropriate string name and variables.
- The syntax of commands sent to the VSMMAR must be exactly correct to be accepted. Confirm all intended setting changes by sending a request command to output the new settings and reviewing those settings before committing the changes via the $RBT: command.
- NOTE: While all this capability exists, “programming” the VSMMAR via ASCII commands can be tedious. Once the “Dashboard” tool supports the VSMMAR, consider using that tool instead to make system changes and to monitor the VSMMAR. The Dashboard tool, written by Rick Bell, hides all of this complexity behind a very easy to use graphical interface.

## APPENDIX A: RECEIVING DATA FROM THE VSR SYSTEM DEVICES:

Messages which will be output by the VSMMAR:
AST; -- ALTERNATOR STATUS

CPE; -- CHARGE PROFILE ENTRY
SCV; -- SYSTEM CONFIGURATION SST; -- SYSTEM STATUS
FLT; -- FAULTED
AOK; -- ACKNOWLEDGE
DBG; -- DEBUG
RST; -- RESET

All status outputs are suspended during the receiving and processing of a command string. In this way, a command which expects a response (for example: $RSC:) can be assured the next string sent back by the regulator is the response to the request command (though one should still do error checking and validation, as the simple regulator will often just ignore commands which have syntax errors) .

Formats are all in clear, if not long, ASCII strings using comma-separated fields. Note the presence of double commas (separated by a space) between major ‘sections’; this is to simplify manual reading of the strings. Each string is delivered as one continuous line, terminated by a CR/LF.

Additional details of each output string may be discovered by examine the command string for changing those parameters.

### AST; ALTERNATOR STATUS

AST: “AST;, Hours, , BatVolts, AltAmps, BatAmps, SystemWatts, ,TargetVolts, TargetAmps, TargetWatts, AltState, ,BTemp, ATemp, ,RPMs, , AltVolts, FTemp, FAmps, FLD%”

Hours: | Time regulator has been powered up, in hours and fraction (to 2 digits) of hours.
BatVolts: | Derived Battery Volts, in volts and fractions of volts (to 1mV resolution). Used to decide
| change mode changes.
AltAmps: | Measured Alternator Amps, in Amps and fraction of Amps (to 1/10th of an Amp)
BatAmps: | Measured Battery Amps (you are using both shunts right?) being used to decide charge
| modes.
| Voltage and current readings made by the VSMMAR are directly reported as
| AltVolts and AltAmps.
SystemWatts: | Current measured System Watts being delivered.
TargetVolts: | Volts the regulator is attempting to bring the battery to. This value is the actual voltage
| value being driven to and reflects the adjusted charge profile entry (CPE) and the sysVolts
| index value.
TargetAmps: | Amps the regulator will limit the alternator to. This value is the actual amperage being
| driven to and reflects the derating, half power mode adjustments, and or SCUBA-mode
| adjustments. Note: If the VSMMAR is configured with no limits for alternator amps and/or
| system watts a self-imposed limit of 1,000A / 15,000W is set as the maximum values. AST;
| will report these working values. To use on larger systems, you will need to modify the
| source code and proceed at your own risk.
TargetWatts*: | Watts the regulator is actually working to limit the system to.
ChargingState: | Current state of the Alternator, encoded as follows:
| 0 = unknown, 1 = disabled, 2 = faulted, 3 = faulted, reduced load, 4 = sleeping,
| 10 = warm-up, 11 = ramping, 12 = determining alternator capacity,
| 20 = bulk charge, 21 = acceptance charge, 22 = overcharge
| 30 = float charge, 31 = forced float charge,
| 32 = LiFePO forced shutdown, 36 = post float, 38 = equalize
BTemp: | Measured temperature of NTC sensor attached to bat temp port, in degrees.
| -99 indicates temperature has not been measured, NTC sender has failed or is not attached.
ATemp: | Measured temperature of NTC sensor attached to alt temp port, in degrees C.
| -99 indicate temperature has not been measured, or NTC sender has failed.
| -100 indicates the Alternator temp NTC probe is shorted (to select half-power mode)

RPMs: | Measured RPMs of engine (Derived from alternator RPMs and the engine/alternator drive ratio)
AltVolts: | Measured alternator volts, in volts and fractions of volts (to 1mV resolution)
FET Temp: | The temperate of the FETs in degrees C. -99 indicated FET temperate cannot be measured.
Field Amps: | This is a measurement of the current (amperage) being delivered to the field.
| -99 indicated field current is not being measured.
Field %: | % (0..100%) field is being driven.

### CPE; CHARGE PROFILE ENTRY

In response to RCP: command, the CPE string displays the current values of a charge profile entry (CPE). Special note on charge profile entries: All voltage and current values in charge profile tables are displayed in their normalized ’12-volt’ values. See Defining Charging Voltages and Amps for additional information.

“CPE;, n, ACPT_BAT_V_SETPOINT, EXIT_ACPT_DURATION, acptEXIT, reserved_1, , LIMIT_OC_AMPS, EXIT_OC_DURATION, EXIT_OC_VOLTS, reserved_2, ,FLOAT_BAT_V_SETPOINT, LIMIT_FLOAT_AMPS, EXIT_FLOAT_DURATION, FLOAT_TO_BULK_AMPS, FLOAT_TO_BULK_AHS, FLOAT_TO_BULK_VOLTS, , EXIT_PF_DURATION, PF_TO_BULK_VOLTS, PF_TO_BULK_AHS, ,EQUAL_BAT_V_SETPOINT, LIMIT_EQUAL_AMPS, EXIT_EQUAL_DURATION, EXIT_EQUAL_AMPS, , BAT_TEMP_1C_COMP, MIN_TEMP_COMP_LIMIT, BAT_MIN_CHARGE_TEMP, MaxCharge”

n: | Charge Profile number is being displayed/returned (1..8)
ACPT_BAT_V_SETPOINT: | Target battery voltage during bulk and acceptance phases
EXIT_ACPT_DURATION: | Time limit to stay in acceptance phase – in minutes.
EXIT_ACPT_AMPS: | Amp limit to trigger exiting acceptance mode
reserved_1: | Reserved for future use. Nothing implemented yet. Displays 0.
LIMIT_OC_AMPS: | Max Amps which will be supplied by during OVERCHARGE mode.
EXIT_OC_DURATION: | Time limit to stay in overcharge phase – in minutes.
EXIT_OC_VOLTS: | Target battery voltage during overcharge phase

reserved_2: | Reserved for future use. Nothing implemented yet. Displays 0.

FLOAT_BAT_V_SETPOINT: Target battery voltage during float phase

LIMIT_FLOAT_AMPS: Max amps which will be supplied by during float phase.

EXIT_FLOAT_DURATION: Time limit to stay in float mode – in minutes.

FLOAT_TO_BULK_AMPS: Amp limit to trigger resumption of bulk charge mode

FLOAT_TO_BULK_AHS: Amp hours withdrawn after entering float to trigger resumption of bulk charge

FLOAT_TO_BULK_VOLTS: Volt limit to trigger resumption of bulk charge mode

Note: If the regulator is in forced_float mode via a FEATURE-IN port, then none of the above checks to exit float mode (for example, EXIT_FLOAT_DURATION) will be performed. However, regulation will still occur to FLOAT_BAT_V_SETPOINT and LIMIT_FLOAT_AMPS.

EXIT_PF_DURATION: | Time limit to stay in post float mode – in minutes, before resuming float charge
PF_TO_BULK_VOLTS: | Battery Voltage that will trigger resumption of float charge mode
PF_TO_BULK_AHS: | Amp hours withdrawn after entering post float to trigger resumption directly to bulk charge mode

EQUAL_BAT_V_SETPOINT: Target battery voltage during equalize phase

LIMIT_EQUAL_AMPS: Current limit of alternator while in equalize mode

EXIT_EQUAL_DURATION: Time limit to stay in equalize mode – in minutes.

EXIT_EQUAL_AMPS: Amp limit to trigger exiting equalize mode

BAT_TEMP_1C_COMP:

Temperature compensations value per 1-degree C (normalized to ’12-volt’ battery)

MIN_TEMP_COMP_LIMIT: Minimum temperate at which temperature compensation will still be applied. In degrees C

BAT_MIN_CHARGE_TEMP: Minimum temperature at which charging will be allowed. Below this temperature, regulator will be forced into float mode.

BAT_MAX_CHARGE_TEMP:

Maximum temperate at which charging will be allowed. Above this temperature, regulator will be forced into float mode.

### SCV; SYSTEM CONFIGURATION

"SCV;, CONFIG_LOCKOUT, REVERSED_BAT_SHUNT, REVERSED_ALT_SHUNT, SV_OVERRIDE, BC_MULT_OVERRIDE, CP_INDEX_OVERRIDE, , ALT_TEMP_SETPOINT, ALT_AMP_DERATE_NORMAL, ALT_AMP_DERATE_SMALL_MODE, ALT_AMP_DERATE_HALF_POWER, ALT_PULLBACK_FACTOR, , ALT_AMPS_LIMIT, ALT_WATTS_LIMIT, , ALTERNATOR_POLES, ENGINE_ALT_DRIVE_RATIO, BAT_AMP_SHUNT_RATIO, ALT_AMP_SHUNT_RATIO, , ALT_IDLE_RPM, MIN_FIELD_TACH_PWM, ENGINE_WARMUP_DURATION, REQURED_SENSORS);

CONFIG_LOCKOUT: | Current lockout level. (0..2), see $SCO: command.
Reserved: | Always = 0; (Was Favor 32v system detection over 24/48v?)
REVERSED_BAT_SHUNT: | 0 or 1: Reverse polarity of battery shunt readings? (1 = yes)
REVERSED_ALT_SHUNT: SV_OVERRIDE: | 0 or 1: Reverse polarity of alternator shunt readings? (1 = yes) System voltage auto-detect (=0), or force (1.0x .. 2.0x → 12v .. 24v)
BC_MULT_OVERRIDE: | Override battery Capacity DIP switches (Dip 4,5). (0.00 = No)
CP_INDEX_OVERRIDE: | Override charge profile DIP Switches (Dip 1,2,3) (0 = No)
ALT_TEMP_SETPOINT: | Target max running temperature for alternator, in degrees C

ALT_AMP_DERATE_NORMAL: Normal amp reduction (de-rating) fraction

ALT_AMP_DERATE_SMALL_MODE: Amp reduction (de-rating) fraction when in small alternator mode

ALT_AMP_DERATE_HALF_POWER: Amp reduction (de-rating) fraction when in half-power mode.

ALT_PULLBACK_FACTOR: Pull-back factor, for reducing field drive at lower RPMs.

ALT_AMPS_LIMIT: | Defined alternator size, or -1 to enable auto-sizing. Set this = 0 for installations where alternator sizing is not to be regulated (for example in battery-focused installations). Note: During startup, and unless defined, this value will present: 1,000
ALT_WATTS_LIMIT: | Defined system size, or -1 to enable auto-sizing. Set this = 0 for installations where watts loading is not to be regulated (for example in a battery-focused installation). Note: During startup, and unless defined, this value will present: 15,000
ALTERNATOR_POLES: | Number of poles on alternator

ENGINE_ALT_DRIVE_RATIO: Ratio of engine and alternator drive pulley

BAT_AMP_SHUNT_RATIO:

ALT_AMP_SHUNT_RATIO:

Battery Shunt ratio in amps / mV

Alternator shunt ratio in amps / mV

ALT_IDLE_RPM: Idle RPM value used as basis for Field Drive Reduction at lower RPMs.

MIN_FIELD_TACH_PWM: Minimum % of field drive that will be applied if tach mode is enabled.

ENGINE_WARMUP_DURATION: Number of seconds after power on before entering ramping mode.

REQURED_SENSORS: Key indicating critical sensors which have been configured via the $SCA: command

### SST; SYSTEM STATUS

“SST; , firmwareVersion, , smallAltMode, tachMode, , cpIndex, systemAmpMult, systemVoltMult, , altCapAmps, altCapRPMs, , Accumulated Amp Hours, Accumulated Watt Hours, , Forced Tach Mode”

firmwareVersion: Firmware revision identifier. Will have format of “AREG” followed w/o a space by the version number. E.g., “AREG1.3M”

SmallAltMode: | 0 or 1, has the user selected Small Alternator Mode? (1 = yes)
tachMode: | 0 or 1, has user selected Tach Mode? (1 = yes)
cpIndex: | Which charge profile (1..8) is currently being used?
systemAmpMult: | What adjustment factor for Battery Amp Hour Capacity (1-10x) is currently being
used?
Fractional values may also be used to fine tune the system to a given battery size. This needs to be entered via the $SCO: command.
systemVoltMult: Detected system voltage. Adjusts target charge profile volts per the following table:
SysVolt | Detected System Voltage | Charge Profile VOLTAGE Adjustment Factor
1 | 12v | 1x
2 | 24v | 2x
altCapAmps: | If regulator is configured to auto-determine the capacity of the alternator, this
will be the current high-water mark noted.
altCapRPMs: | RPMs at which that capacity was noted.

Accumulated Amp
Hours:

The number of amp-hours that have been produced in the current charge cycle.

Accumulated
Watt Hours:

The number of Watt-Hours produced in the current charge cycle.

Forced Tach Mode: 0 or 1, has user forced tach-mode on via the $SCT: command.

### FLT; FAULTED

FLT: “FLT;, FaultCode, RequiredSensorStatus ”

System has Faulted, fault code number (See source code for details.)

RequiredSensorStatus is a combined number following the pattern as defined by the $SCA command and detailed in the Required Sensor section on page number 26

Following this, the AST, SST and SCV will be printed, as well as the currently active CPE.

### AOK; ACKNOWLEDGE

Sent after a successfully receiving change command ($CPx, or $SCx), or $EDB

### DBG; DEBUG

Special string with extra internal parameters. See Source code for details of Debug String

### RST; RESET

Regulator has been requested to reset. This can take up to 10 seconds to complete.

## APPENDIX B: SENDING DATA TO THE REGULATOR:

All commands begin with the character `$’, contain 3 letters (CAPS) followed by a `:’ and then parameters relevant to the command. All must end with a CR (or CR/LF) or may optional be terminated with the character `@’ (this is to accommodate a bug in the Arduino IDE that does not send CR nor LF at the end of entered strings). A complete ‘string’ must be received within 60 seconds from the `$’ to the ending `@’/CR/LF, or the regulator will abort the capture of that string command and begin looking for a new `$’ starting character. (See #define IB_BUFF_FILL_TIMEOUT 60000UL in OSEnergy_Serial.h).

Sending communications TO the regulator:

$CPA:n - Change ACCEPT parameters in CPE user entry n (n = 7 or 8) $CPO:n - Change OVERCHARGE parameters in CPE user entry n (n = 7 or 8) $CPF:n - Change FLOAT parameters in CPE user entry n (n = 7 or 8)

$CPP:n - Change POST-FLOAT parameters in CPE user entry n (n = 7 or 8)

$CPE:n - Change EQUALIZE parameters in CPE user entry n (n = 7 or 8) $CPB:n - Change BATTERY parameters in CPE user entry n (n = 7 or 8) $CPR:n - RESTORES Charge Profile ‘n’ to default values
$RAS: - Request All Status back
$RCP:n - Request to send back CPE entry #N (n=1..8) **
$RCP:0 - Request to send back current selected CPE**
$SCA: - Changes ALTERNATOR parameters in System Configuration table $SCT: - Changes TACHOMETER parameters in System Configuration table $SCO: - Override features
$SCR: - RESTORES System Configuration table (+ Bluetooth) to default

$MSR: - RESTORE all parameters (to as defined at program compile time). $EDB: - Enable DeBug serial strings

$RBT: - ReBooT system

$FRM: - Force Regulator Mode

Defining Charging Voltages and Amps – All volts and amps are represented for a normalized 12-volt 500Ah battery and are automatically scaled depending on the sampled battery voltage at startup and the setting of the battery capacity DIP switches.

Note that the MAXIMUM length of a string is fixed at 70 characters, including the line termination character(s). When assembling a command to send make sure not to exceed this length, remove any extra spaces if present to assure total length is under 70 characters.

**Note on Requesting Status commands. All ‘Request’ commands will reply via the USB Serial port.

$CPA:n Change Acceptance parameters in CPE user entry n (n = 7 or 8)
This command (with its parameters) will cause the acceptance (and bulk) portion of a charge profile entry (CPE) to be updated. Parameters must be in the following order and include comma “,” separators where indicated. Extra spaces before and/or after the parameters are allowed.

$CPA:n <ACPT_V_BAT_SETPOINT>, <EXIT_ACPT_DURATION>, <EXIT_ACPT_AMPS>,<Reserved>

n: (7 → 8) ‘n’ is the charge profile table entry that will be modified. Use range 7 to 8.

ACPT_V_BAT_SETPOINT: <FLOATING POINT NUMBER (0.0 → 20.0) > Voltage the Regulator will use during acceptance phase. When this voltage has been reached, the regulator will transition from bulk to acceptance phase. This value is a floating-point number and entered for a normalized 12-volt system (See note: Defining Charging Voltages and Amps)

EXIT_ACPT_DURATION: <WHOLE NUMBER (minutes: 0 → 600 (10 hours)) > After entering acceptance phase, a timer will be started. After ‘EXIT_ACPT_DURATION’ minutes have expired acceptance mode will exit and the regulator will move to overcharge mode, if overcharge mode is defined for the charge profile, otherwise the regulator will move to float mode. Setting ‘EXIT_ACPT_DURATION’ = 0 will disable time based exiting of acceptance mode and only amp-based monitoring will be used.

EXIT_ACPT_AMPS: <WHOLE NUMBER (-1 → 200)> After entering acceptance phase, delivered amps will be monitored and if they fall to (or below) ‘EXIT_ACPT_AMPS’ acceptance mode will exit and the regulator will move to overcharge mode, if overcharge mode is defined for the charge profile, otherwise the regulator will move to float mode. This is provided that the battery voltage is at the target VBat Set Point above (to prevent early exiting from low amps being delivered as a result of the engine slowing down to say very slow idle).

Setting ‘EXIT_ACPT_AMPS’ = 0 will disable amp-based exiting of acceptance mode and only time monitoring to ‘ExitDuration’ will be used as the exit criteria.

Setting ‘EXIT_ACPT_AMPS’ = -1 will disable amp-based exiting of acceptance mode and time monitoring of ‘EXIT_ACPT_AMPS’will be used as above. In addition, when the time spent in acceptance mode has exceed 5x the duration spent in bulk mode, the regulator will also trigger an exit. This is known as “adaptive acceptance”).

Note: If you set BOTH ‘EXIT_ACPT_AMPS’ and ‘EXIT_ACPT_AMPS’ = 0, the regulator will bypass acceptance mode.

Reserved: <0> Placeholder for future. No action defined at this time. Must be set to 0.

Examples:
$CPA:7 14.5, 200, 40, 0 @ | #7: 14.5VOLTS, EXIT AFTER 200 MINUTES OR UNDER 40AMPS
$CPA:8 12.4, 0, 20, 0@ | #8: 12.4 VOLTS, EXIT ONLY ON AMPS UNDER 20

$CPA:810.4,0,20,0@ | #8: 10.4 VOLTS, EXIT ONLY ON AMPS UNDER 20 (SHOWN WITH OPTIONAL ‘@’ FOR ARDUINO IDE TERMINAL SUPPORT)

$CPO:n Change Overcharge parameters in CPE user entry n (n = 7 or 8)
This command (with its parameters) will cause the overcharge portion of a Charge Profile Entry (CPE) to be updated. Parameters must be in the following order and include comma “,” separators where indicated. Extra spaces before and/or after the parameters are allowed.

$CPO:n <LIMIT_OC_AMPS>, <EXIT_OC_DURATION>, <EXIT_OC_VOLTS>, <Reserved>

n: (7 → 8) ‘n’ is the charge profile table entry that will be modified. Use range 7 to 8.

LIMIT_OC_AMPS: <WHOLE NUMBER (0 → 50)> After entering overcharge phase, delivered amps will be monitored and regulated to ‘LIMIT_OC_AMPS’ . Setting LIMIT_OC_AMPS’ = 0 will disable overcharge mode.

EXIT_OC_DURATION: <WHOLE NUMBER (minutes: 0 → 600 (10 hours)) > After entering overcharge phase, a timer will be started. After ‘EXIT_OC_DURATION’ minutes have expired, overcharge mode will exit and the regulator will move to float mode. Setting ‘EXIT_OC_DURATION’= 0 will disable overcharge mode.

EXIT_OC_VOLTS: <FLOATING POINT NUMBER (0.0 → 20.0) > Once battery voltage reached ‘EXIT_OC_VOLTS’, overchage phase will be exited. This value is a floating-point number and entered for a normalized 12-volt system (See: Defining Charging Voltages and Amps). Setting ‘EXIT_OC_VOLTS’ = 0 will disable OVERCHAGE mode.

Reserved: <0> Place holder for future. No function at this time. Must be set to 0.

$CPF:n Change float parameters in CPE user entry n (n = 7 or 8)
This command (with its parameters) will cause the float portion of a charge profile entry (CPE) to be updated. Parameters must be in the following order and include comma “,” separators where indicated. Extra spaces before and/or after the parameters are allowed.

$CPF:n <FLOAT_BAT_V_SETPOINT>, <LIMIT_FLOAT_AMPS>, <EXIT_FLOAT_DURATION>, <FLOAT_TO_BULK_AMPS>, <FLOAT_TO_BULK_AHS>, < FLOAT_TO_BULK_VOLTS >

n: (7 → 8) ‘n’ is the charge profile table entry that will be modified. Use range 7 to 8.

FLOAT_BAT_V_SETPOINT: <FLOATING POINT NUMBER (0.0 → 20.0) > Voltage the regulator will use during float phase. This value is a floating-point number and entered for a normalized 12-volt system (See note: Defining Charging Voltages and Amps)

LIMIT_FLOAT_AMPS: <WHOLE NUMBER (-1 → 50)> While in float phase delivered amps will be monitored and regulated to ‘LIMIT_FLOAT_AMPS s’ . Setting ‘LIMIT_FLOAT_AMPS’ = -1 will disable this feature and only ‘FLOAT_BAT_V_SETPOINT’ will be regulated. 1

EXIT_FLOAT_DURATION: <WHOLE NUMBER (0 → 30000 (500 hours)) > After entering float phase, a timer will be started. After ‘EXIT_FLOAT_DURATION’ minutes have expired float mode will exit and the regulator will move to postfloat mode. Setting ‘EXIT_FLOAT_DURATION’ = 0 will cause the regulator to remain in float mode unless triggered by another exit criteria.

FLOAT_TO_BULK_AMPS: <WHOLE NUMBER (-300 → 0)> While in float mode, if ‘FLOAT_TO_BULK_AMPS’ are exceeded it is an indication that a large load has been placed on the battery and current is being withdrawn, the regulator will restart a charge cycle, looping back to bulk mode. Setting ‘FLOAT_TO_BULK_AMPS’ = 0 will disable this feature.

FLOAT_TO_BULK_AMPS is most useful in the case where there is an amp shunt is placed on the battery, as when the amp draw from the battery exceeds FLOAT_TO_BULK_AMPS, it is a clear indication energy is being drawn from the battery. In this case, set FLOAT_TO_BULK_AMPS equal to the number of amps being drawn from the battery that should be used to trigger a return to bulk mode.

In cases where the amp shunt is installed on the Alternator, this can also be of use by sizing FLOAT_TO_BULK_AMPS to a value slightly above expected house load values. However, perhaps a better indication is to set this to =0, and use FLOAT_TO_BULK_VOLTS.

FLOAT_TO_BULK_AHS: <WHOLE NUMBER (-250 → 0)> After entering float mode if the accumulated number of amp hours removed from the battery exceeded ‘FLOAT_TO_BULK_AHS’ the regulator will re-start a charge cycle, looping back to bulk mode. Setting ‘FLOAT_TO_BULK_AHS’ = 0 will disable this feature

This is another way to indicate the need to restart charging of the battery, and perhaps a better approach than using raw ‘FLOAT_TO_BULK_AMPS’, but it is only usable with an amp shunt placed on the battery.

FLOAT_TO_BULK_VOLTS: <WHOLE NUMBER (0.0 → 20.0)> While in float mode, if battery voltage drops below ‘FLOAT_TO_BULK_VOLTS’ we assume this indicates a large load has been placed on the system and the regulator will restart a charge cycle, looping back to bulk mode. Setting ‘FLOAT_TO_BULK_VOLTS’ = 0 will disable this feature.

In determining to exit float mode, a rolling average value for measured amps and volts is used. This way short term events (e.g., a surge of a refrigerator starting up and before the alternator can respond) will not pull the regulator out of float mode. Note also that the revert amp –hours is a negative value and measures the number of amp hours removed from the battery after entering float mode.

$CPP:n Change Postfloat parameters in CPE user entry n (n = 7 or 8)
This command (with its parameters) will cause the postfloat portion of a charge profile entry (CPE) to be updated. Parameters must be in the following order and include comma “,” separators where indicated. Extra spaces before and/or after the parameters are allowed.

$CPP:n <EXIT_PF_DURATION>, <PF_TO_BULK_VOLTS>, <PF_TO_BULK_AHS>

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

EXIT_PF_DURATION: <WHOLE NUMBER (minutes: 0 → 30000 (500 hours)) > After entering postfloat phase, a timer will be started. After ‘EXIT_PF_DURATION’ minutes have expired v mode will exit and the regulator will revert to float phase. Setting ‘EXIT_PF_DURATION’ = 0 will disable postfloat mode revering to float charge immediately.

PF_TO_BULK_VOLTS: <<FLOATING POINT NUMBER (0.0 → 20.0)> While in postfloat mode, if the system battery voltage drops below ‘PF_TO_BULK_VOLTS ’ it is an indication that a large load has been placed on the system and the regulator will re-start a charge cycle, looping back to bulk mode. Setting ‘PF_TO_BULK_VOLTS’ = 0 will disable this feature.

PF_TO_BULK_AHS: <WHOLE NUMBER (-250 → 0)> After entering postfloat mode if the accumulated number of amp hours removed from the battery exceeded ‘PF_TO_BULK_AHS’ the regulator will re-start a charge cycle, looping back to bulk mode. Note that this trigger goes directly to bulk, as opposed to back to
float mode. Setting ‘PF_TO_BULK_AHS‘= 0 will disable this feature

$CPE:n Change Equalize parameters in CPE user entry n (n = 7 or 8)
This command (with its parameters) will cause the Equalize portion of a charge profile entry (CPE) to be updated. Parameters must be in the following order and include comma “,” separators where indicated. Extra spaces before and/or after the parameters are allowed.

$CPE:n < EQUAL_V_BAT_SETPOINT >, < LIMIT_EQUAL_AMPS’ >, < EXIT_EQUAL_DURATION >, < EXIT_EQUAL_AMPS >

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

EQUAL_V_BAT_SETPOINT: <FLOATING POINT NUMBER (0.0 → 25.0) > Voltage the regulator will use during equalize mode. This value is a floating-point number and entered for a normalized 12-voly system (See note: Defining Charging Voltages and Amps). Setting ‘EQUAL_V_BAT_SETPOINT’ = 0 will disable equalize mode.

LIMIT_EQUAL_AMPS: <WHOLE NUMBER (0 → 50)> Optional additional current limit while in equalize phase; the regulator will cap delivered amps to ‘LIMIT_EQUAL_AMPS’ . Setting ‘LIMIT_EQUAL_AMPS’ = 0 will disable this amperage capping.

EXIT_EQUAL_DURATION: <WHOLE NUMBER (minutes: 0 → 240 (4 hours)) > After starting an equalize phase, a timer will be started. After ‘EXIT_EQUAL_DURATION’ minutes have expired, equalize will terminate and the regulator will enter float mode. Setting ‘EXIT_EQUAL_DURATION’ = 0 will disable equalize mode.

EXIT_EQUAL_AMPS: <WHOLE NUMBER (0 → 50)> During equalize mode delivered amps will be monitored and if it falls to (or below) ‘EXIT_EQUAL_AMPS’ , equalization will be terminated and the regulator will move to float mode. Note that as a precaution, battery voltage is not checked when sampling Equalization Exit Amps (as it is in acceptance and overcharge modes). It is up to the operator to keep the engine speed up and allow for a full equalization session to occur. Setting ‘EXIT_EQUAL_AMPS’ = 0 will disable amp-based exiting of equalize mode and only time monitoring will be used.

$CPB:n Change Battery parameters in CPE user entry n (n = 7 or 8)
This command (with its parameters) will cause the remaining portion of a charge profile entry (CPE) to be updated. Parameters must be in the following order and include comma “,” separators where indicated. Extra spaces before and/or after the parameters are allowed.

$CPB:n <VBat Comp per 1OC>, < Min Comp Temp >, <Min Charge Temp>, <Max Charge Temp>

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

VBat Comp: <FLOATING POINT NUMBER (0.0 → 0.1)> This is used to adjust all target VBat voltages based on the current battery temperature in 1 degree C increments. This value is a floating-point number and entered for a normalized 12-volt system at 25c. (See note: Defining Charging Voltages and Amps). Set = 0.0 to disable temperature-based voltage compensation.

Min Comp Temp: <WHOLE NUMBER (-30 → 40)> Additional compensation to battery target voltages will be stopped when the battery is at or below this temperature in degrees C.

Min Charge Temp: <WHOLE NUMBER (-50 → 10) > If the battery drops below this temperature, the system will be forced into float mode to protect it.

Max Charge Temp: <WHOLE NUMBER (20 → 95) > If the battery reaches this temperature, the system will be forced into float mode to protect it. If the battery temperature continues to raise, the system may eventually fault based on the value of #define FAULT_BAT_TEMP in the source code (60c (140F) by default).

$CPR:n - RESTORES Charge Profile ‘n’ to default values
Restores to default (values at compile time) charge profile entry (CPE) ‘n’. After entry ‘n’ is restore, the regulator will be restarted automatically.

$CPR:n

n: (7 → 8) ‘n’ is the charge profile table entry that will be restored. Use range 7 to 8.

$RAS: Request All Status back
This command will instruct the VSMMAR to send out, via the USB erial port, a copy of the all known status strings. It is useful for external applications to capture the current status without needing to await the arrival of each string (which could take several minutes or more, depending on how status strings are paced out).

$RAS:

After all status strings have been sent, “AOK” will be sent to indicate the end.

$RCP:n Request to send back CPE entry #N (n=1..8) **
This command will instruct the VSMMAR to send out, via the USB Serial port, the saved contents of the CPE entry N, where N is a number from 1 to 8. See “CPE: Charge Profile Entry” for description of resulting transmission.

$RCP:n

$RCP:0 - Request to send back current selected CPE**
Special version of request for CPE, this will send back the currently selected (via the DIP switches) CPE.

$RCP:0

Note, the CPE entry sent back in response to a $RCP: command will reflect the current values contained in flash memory which may not match what the regulator is currently working with. If a CPE has been modified and saved to flash, those modifications will be reflected. However, until the VSMMAR is rebooted it will not utilize those values. For current active targets being used, look at AST; and SCV; status strings.

Note on Change Requests to Charge Profiles: The source code currently will allow only charge profile 7 or 8 (the two customizable entries) to be modified via an ASCII command. This is to reduce the potential for major errors in the regulator. If you wish to modify other charge profiles, the source code will need to be revised to either change the default tables, or alter the trap to allow changes via ASCII beyond entry 7 or 8.

Also, take great care in setting these values, especially the exiting time and amp thresholds. Some of these thresholds can be disabled by setting to 0, disabling that threshold test. If both amps & time values are disabled, it is possible for the regulator to stay in a full charge state indefinitely, likely causing damage to the battery. As the VSMMAR may be deployed with either a battery shunt or alternator shunt, of with both a battery and alternator shunt (which is the recommended configuration), the CPE entries will behave differently depending on which deployment model is used. And some entries might have no meaning. Great Flexibility results in Great Responsibility…

All change profile commands will reply with “AOK;” if the command was processed successfully. However, to assure the changes are stored and used, the regulator must be reset using the $RBT: command after all changes have been made.

$SCA: Changes Alternator parameters in System Configuration table
Used to update the system configuration table entries associated with the alternator.

$SCA: <reserved>, < Alt Target Temp >, <Alt Derate (norm) >,<Alt Derate (small) >,
<Alt Derate (half) >, <PBF>, <Alt Amp Cap >, <System Watt Cap. >, < BAT_AMP_SHUNT_RATIO >,
< BAT_AMP_SHUNT_RATIO>, < REVERSED_BAT_SHUNT>, < REVERSED_ALT_SHUNT: >, <Idle RPMs>,<Warmup Delay>,<RequiredSensors>

Reserved: <WHOLE NUMBER = 0> Not used. Must be set to 0.

Alt Target Temp: <WHOLE NUMBER (15 → 120)> Operating temperature under which the regulator should attempt to keep the alternator. If the alternator temperature exceeds this value, the regulator will reduce field current to allow the alternator to cool off. If the Alternator temperature continues to rise and exceeds this temperature by 10% (as defined by #define FAULT_ALT_TEMP) the regulator will fault out and stop all power production.

Alt Derate(norm), Alt Derate(small),
Alt Derate(half): <FLOATING POINT NUMBER (0.10 → 1.00) > These derating values are used to limit the alternator’s maximum current output to some percentage (10% to 100%) of its demonstrated capability (see Alt Amp Cap). The three values correspond to the following alternator modes:
- Normal - Condition when neither of the other modes is selected.
- Small Alternator Mode – selected via DIP switch 6 (or the override via $SCT command)
- Half-Power Mode – Selected by shorting the alternator NTC temperature sensor wires.

In operation, de-rating values are applied to both the Alt Amp Cap as well as the internal maximum field PWM drive. In this way, a smaller alternator is protected, even if an alternator shunt is not connected.

PBF: < INTEGER (-1 → 10)> Pullback factor for reducing Field Drive at lower RPMs. If the VSMMAR is able to determine RPMs (via the stator wire), the Alternator Field Drive will be reduced when the regulator detects the engine is at Idle. At idle the max PWM will be capped at around 1/4 of full field, which should result in some current bring produced. As RPMs are increased, this ‘Field Drive Capping’ will slowly be removed. PBF determines how quickly this pull-back is scaled off.

Set = 0 to disable this feature.

Set = -1 (DEFAULT) to cause Field Drive to be reduced to a maximum of 70% drive in the case where the VSMMAR is no longer able to measure RPMs via the stator-in signal. This might be, for example, where an engine is operating at extremely low RPMs, below the cut-in point for the alternator. Or where the engine is no longer running. The 70% limit will only be enabled if at one time during operation the regulator was able to measure RPMs successfully.

For many engine / alternator combinations the default value of 1 should result in good operations. However, if you have installed a large alternator on a rather modest sized engine, you might notice the engine struggles when trying to increase RPMs from idle. In that case, increase the PBF value. A factor of 8x or so might be needed in the case of a small sailboat engine with a large 150-amp or greater alternator (consider also using the Alt Amp Cap and/or System Watts Cap capabilities as well to restrict maximum engine loading at higher RPMs).

If the engine has a large capacity relative to the alternator size, consider reducing the PBF to 1. Doing so will allow a greater production of amps while at idle, while at the same time preventing the alternator from being driven at Full Field during low RPMs (and hence low cooling)

Finally, if your system matches an engine with great capability, and the alternator has good cooling / heat management – you can set the PBF factor = 0 to disable any capping of field drive while the engine is at idle. This will allow for maximum alternator output at idle, however if the regulator is enabled but the engine is not actually running, field drive will increase to Full Field until a fault check causes the regulator to reset. Do not leave the ‘ignition’ in the on position, without the engine actually running to prevent this situation. It would be advisable to assure there is a temperate sensor attached to the alternator in this case – to prevent unintended overheating during prolonged idle periods.

Note: Field Pullback is dependent upon the stator sensing wire being connected to the alternator. If the regulator is unable to reliability sense RPMs, all idle pullback features will be disabled. Note also that one should make sure to configure the tachometer via the $SCT: command.

Alt Amp Cap: <WHOLE NUMBER ( -1→ 500 ) > This regulator will limit the amperage output of the alternator to this value, after applying the ‘Alt Derate xxx’ factors. There is no adjustment made to this value based on system voltage or selection of system battery size – the values declared will be used directly. A special feature is enabled by setting this = -1: the regulator will drive the alternator as hard as it can for a short period of time when first entering bulk phase and in this way will auto-sample the alternator size based on its capabilities.

Note: Alt Amp Cap is a feature intended to be used in alternator-centric deployments (refer to the VSMMAR Reference Manual) and should only be defined if there is a current shunt located at the alternator. During operation the regulator will limit measured amps to Alt Amp Cap value. During reduced power modes (i.e., – Half-Power mode) the amperage allowed will be further limited by the appropriate scaling factor.

For battery-Centric deployments this value should be set = 0, thereby disabling measured amperage limits of the alternator. With amperage limits disabled, reduced power modes will apply the scaling factor to the PWM duty cycle. It should be noted that there may not be a direct relation between reductions in PWM duty cycles and delivered amps – care should be used when setting up the system. (Default = 0, disabled)

System Watts Cap: <WHOLE NUMBER ( -1→ 20000 )> The regulator will limit the system wattage to this value. Its primary use is to protect the driving engine and/or belts – by limiting the maximum
amount of work the engine is asked to do on behalf of the alternator. (Work being a function of both volts and amps, hence watts). It may also be used to limit the total amount of power being delivered into the battery by all charging sources. There is no derating or adjustment made to this value based on system voltage or selection of system battery size. System Watts Capacity is used to after applying the ‘Alt Derate xxx’ factors. It is used to protect the alternator from over-current usage. A special feature is enabled by setting this = -1, the regulator will drive the alternator as hard as it can for a short period of time when first entering bulk phase. This will then be used to define the amp Limit of the aternator.

Note on Alt Amps and System Watts: You may set either of these parameters =-1 to allow the regulator to automatically calculate limits based on the sampled capability of the alternator, or set them = 0 to disable that feature. Though these two are interlaced, they are indeed separately monitored and adjustments to the Field PWM are made independently for each.

(Default = 0, disabled)

BAT_AMP_SHUNT_RATIO:
ALT_AMP_SHUNT_RATIO: <WHOLE NUMBER 500 → 20000)> Enter the ratio of your amp measurement shunts in terms of amps / mVolts. e.g., if you have a 250A / 75mV shunt, you would enter

3333 (250/0.075). And you may adjust the number to allow for fine tuning of the amp shunt. e.g., if your shunt has a 3% error, you could enter 3433

Caution: Shunt voltage is limited to +/-80mV. Do NOT exceed this value!

REVERSED_BAT_SHUNT:
REVERSED_ALT_SHUNT: | <WHOLE NUMBER (0, or 1) > Allows software correction if an amp shunt
was wired backwards. Set = 1 and amp readings will have their polarity changed.

Idle RPMs: < INTEGER (0 → 1500)> Used in conjunction with PBF to manage Field Drive at lower RPMs. As
RPMs rise above Idle RPMs, field drive will be increased at a rate determined by PBF. During normal operation, Idle RPMs can be detected automatically by the VSMMAR. However, in more sensitive installations where the management of the alternator Field Drive at low RPMs is critical, additional system reliability can be achieved by defining the IDLE RPMs value to be used in all calculations. In extreme installations (for example, a very small engine with large efficient alternator), Idle RPMs may be defined artificially high; doing so will cause the regulator to increases its pullback of Field Drive during low RPM operations.

Set = 0 (DEFAULT) to enable ‘auto’ determination of Idle RPM.

Warmup Delay: <WHOLE NUMBER ( seconds: 15 → 600 ) > Hold-off period when regulator is first powered on before it will begin to apply a load to the engine. This is the number in seconds of delay the regulator will remain in pre-ramp mode before moving into ramping mode. Default = 15 seconds.

Required Sensors: <WHOLE NUMBER ( 0 → 255 ) > Many capabilities depend on the presence of sensors. Battery compensation requires the presence of a battery temperature sensor; Alternator temperature regulation requires the presence of an alternator temperature sensor. If one or more of these sensors are not installed, or fail during operation, results could be less then desired. As a precaution against this, Required Sensors allows the identification of critical sensors for your installation, and if any of them are missing or fail the regulator will take action to reduce demands placed on the system.

Required Sensors allows the identification of critical sensors. It is a number created by summing up the value associated with each potential critical sensor. For example: if you wished to indicate the alternator and battery temperature sensors are critical, you would enter 3 (1+2). The value of 0 disables critical Required Sensor checks and the regulator will utilize other existing fallback modes.
Sensor | Value | Default Action of missing sensor
Alternator Temperature Sensor | 1 | Enable Half-Power mode
Battery Temperature Sensor | 2 | Force to FLOAT mode
Battery Current Shunt | 4 | FAULT regulator (See note**)
Alternator Current Shunt | 8 | FAULT regulator (See note**)

Force FAULT override | 128 | Overrides ‘Default’ action and forces regulator into FAULT mode.

Table 1 - Required Sensor Encoding

If at any time one of the Required Sensors are identified as failed or missing the LED will flash its normal patterns, but in RED. In addition, if a Feature_out port is configured to drive a dash-lamp it will turn on the lamp fulltime indicating a fault.

The VSMMAR may also be configured to cause a non-recoverable FAULT condition, overriding the default actions listed in Table 1 by adding 128 to the summed number. In the prior example of battery and alternator temperatures sensors being critical, sending 131 instead of 3 will cause the regulator to FAULT if either is noted as missing or fails.

Note** It is difficult to determine if an amp shunt has failed vs. if are truly reading zero current. Because of this, the VSMMAR will delay checking for the presence of a working current shunt until after bulk mode has been completed. If at any time during bulk mode a current of greater than 5A was noted, it will be flagged as the shunt being present and working. Once this determination is made no additional checks will be made – as a valid operating condition for the regulator is a true zero current (example, when actively regulating current to zero amps in float mode).

$SCA: will reply with “AOK;” if the command was processed successfully. However, to assure the changes are stored and used the regulator must be reset using the $RBT: command after all changes have been made.

Example: Large alternator powered by large main engine:

- Disable Idle adaptive pullback (alternator has massive cooling capability, and engine has sufficient reserve)
- Adjust amp shunt to 250A/75mV (as appropriate for your shunt)
- Define engine idle @ 550 RPMs
- Must have alternator temperature sensor present, else cause regulator to FAULT
- Leave other values as default (See Appendix D: )

Command Syntax: (color-coded to make it easier to map values to their names)
$SCA: <reserved>, < Alt Target Temp >, <Alt Derate (norm) >,<Alt Derate (small) >, <Alt Derate (half) >, <PBF>, <Alt Amp Cap >, <System Watt Cap. >,
< BAT_AMP_SHUNT_RATIO>,< BAT_AMP_SHUNT_RATIO>, < REVERSED_BAT_SHUNT>, < REVERSED_ALT_SHUNT >, <Idle RPMs>,<Warmup Delay>,<RequiredSensors>

$SCA:0,95,1.0,0.75,0.50,0,0,0,3333,3333,0,0,550,6 0,129@ $RBT:@

Notes: Some versions of the Arduino IDE do not send the correct CR/LF termination – in these cases the ‘@’ symbol (as shown above) may be placed at the end of a line to communicate end-of-command.

Example: Detailed configuration. Large alternator powered by large main engine, 1500AH industrial FLA battery:

- Acceptance @ 14.4v until acceptance current is less than 1% of capacity, 8hr max.
- 8hr Time limit is set as fallback in case of battery current sensing
failure.
13.2v float - revert back if 2% of capacity is removed
15.3v Equalize, 3Hr duration.
- No overcharge nor postfloat phases.
- Allow alternator to operate up to 105c
- 30mV per degree C temperature comp

Command Syntax: (color-coded to make it easier to map values to their names) $SCA: <reserved>, < Alt Target Temp >, <Alt Derate (norm) >,<Alt Derate (small) >, <Alt Derate (half) >, <PBF>, <Alt Amp Cap >, <System Watt Cap. >,
< BAT_AMP_SHUNT_RATI>, < BAT_AMP_SHUNT_RATIO>, < REVERSED_BAT_SHUNT>, < REVERSED_ALT_SHUNT >, <Idle RPMs>,<Warmup Delay>,<RequiredSensors>

$SCA:0,105,1.0,0.75,0.50,0,0,0,3333,3333, 0, 0,550,30,0@
$CPA:7 14.4,480,5,0@
$CPO:7 0,0,0,0@
$CPF:7 13.2,-1,0,0,-10,12.7@ $CPP:7 0,0,0@
$CPE:7 15.3,0,180,0@
$CPB:7 0.030,15,-50,125@
$SCO:7,3,1,0@
$RBT:@

Example: Change warm-up delay to 30 seconds, leaving the rest of the configuration at the default values:

Command Syntax: (color-coded to make it easier to map values to their names)
$SCA: <reserved>, < Alt Target Temp >, <Alt Derate (norm) >,<Alt Derate (small) >,
<Alt Derate (half) >, <PBF>, <Alt Amp Cap >, <System Watt Cap. >, < BAT_AMP_SHUNT_RATIO >,
< BAT_AMP_SHUNT_RATIO>, < REVERSED_BAT_SHUNT>, < REVERSED_ALT_SHUNT >, <Idle RPMs>,<Warmup Delay>,<RequiredSensors>

$SCA:0,90,1.0,0.75,0.50,-1,0,0, 3333, 3333,0,0,0,30@

Note: Any values in the command syntax after the ones you intend to change, can be left out of the command. So here, we did not enter a value for RequiredSensors.

Note: As you can see, setting parameters in this way is very powerful, but quite tedious. Using the Dashboard tool gives you all this power without the tedium. Nonetheless, refer to this guide to understand the parameters in detail.

$SCT: Changes TACHOMETER parameters in System Configuration table
Update calibration ratios and parameters associated with alternator-driven tachometers. It should be noted the regulator will function correctly without changing any of these parameters; you need only change them if you wish to estimate the RPMs of your engine to be reported by the VSMMAR.

$SCT: <Alt Poles>, < Eng/Alt drive ratio >, <Tach Min Field>, <ForceTM>

Alt Poles: | <WHOLE NUMBER ( 2 → 25 )> Number of poles in the alternator.

Eng/Alt Drive Ratio: <FLOATING POINT NUMBER ( 0. 5 → 50 )> Enter the ratio of your engine drive pulley diameter vs. the alternator drive diameter. Example, if your engine has a 7” drive pulley, and the alternator has a 2.6” drive pulley, then enter 2.6923 which is 7.0 / 2.3

Tach Min Field: <WHOLE NUMBER ( -1 → 30 )> This is the percentage value the PWM will be kept at as the minimum drive when the DIP switch has selected Tach Mode. (DIP switch 7) Be very careful with this value as it will set the floor at which the alternator is driven. If that floor is too high, it will prevent the regulator from ‘regulating’, which can result in burning out the battery. This is the actual PWM value sent to the field drive; though it is capped at 30% the full hardware PWM.

Set Tach Min Field = -1 to enable auto-determination. The VSMMAR will monitor the stator signal and when it becomes stable will use that PWM drive value as the floor. Alternatively, set this = 0 to disable any tach field drive even if the DIP switch is turned on.

If a Tach Min Field value is set (any value greater than 0), and Tach Mode is enabled, the regulator will use this value as a minimal field drive percentage, even during the warm-up period. You may have to experiment with this value to get one which matches your system, taking care not to make it too great as that could cause issues with overcharging of your battery.

If a fixed Tech Min Field value is set, the regulator will also hold in the warmup / idle phase until it is able to stably see RPMs, indicating the engine is running. This will prevent the field from being driven any harder in the case of the regulator is powered on via the Enable pin, but the actual engine is not running. Do take note though: if the stator wire is not connected (or has failed), and/or the Tach Min Field % drive value is too low, the regulator will remain in warm-up mode, ‘appearing’ to have failed when in fact it was been instructed to wait until it can see a stator signal.

ForceTM: <0, or 1> Setting the value to 1 will force on Tach Mode, independent of the Tach Mode DIP switch (DIP switch 7). 0 will cause the regulator follow the DIP-Switch. (DEFAULT = 0)

$SCT: will reply with “AOK;” if the command was processed successfully. However, to assure the changes are stored and used the regulator must be reset using the $RBT: command after all changes have been made.

$SCT: will not be recognized if system has been locked-out via the $SCO: command.

$SCO: Override features
Overrides the DIP Switches for charge profile (1,2,3) and battery capacity (4,5) selection. This command also allows the selection of auto detect for system voltage (12v, 24v), or forcing a fixed defined target system voltage.

$SCO: <CP_Index>, <BC_Index >, <SV_Override>, <Lockout>

CP Index: <WHOLE NUMBER ( 0 → 8 )> Which charge profile entry should be used? (1..8). Set = 0 to use DIP switches for selection.

BC Index: < FLOATING POINT NUMBER ( 0.0 → 10.0 )> Which battery capacity multiplier entry should be used against normalized 500Ah battery? (1..4). Set = 0.00 to restore selection to DIP Switch value.

SV Override: < FLOATING POINT NUMBER ( 0.0 → 4.0 )> Enable (by setting = 0.0) or override the auto system voltage detection feature by defining the SV multiplier to be used. Though auto detect is a nice feature, being able to fix the system voltage can improve reliability and allow support for battery voltages which are not a whole number multiple of the ‘12v’ normalized battery used in the CPE tables. The following table shows some common values which may be used:

SV_Override value | Forced System Voltage | Charge Profile VOLTAGE Adjustment Factor
0 | Auto | Auto
1 | 12v | 1x
2 | 24v | 2x

(Set SV Over-ride = 0 to restore auto-selection of 12-volt or 24-volt system voltages)

Lockout: <WHOLE NUMBER ( 0 → 2 )> Security feature: Restricts ability to perform changes and/or provide input to the regulator which can impact how the alternator charges the battery. BE CAREFUL: Once lockout is enabled (value other then 0), it can ONLY be cleared by doing a hardware based master reset (refer to Reference Manual), or re-flashing the firmware with changes to the EEPROM keys. No other command, not even $MSR: will be able to clear a non-zero lockout. Be especially careful with lockout=2, as the ONLY way to recover the regulator from this state will require special programming hardware probes.

0 = No locking out.

1 = Prevent any configuration changes.

2 = Prevent any configuration changes – may NOT be cleared via Feature-in method.

DO NOT SET THE LOCKOUT UNLESS YOU HAVE A VERY GOOD REASON TO AND UNDERSTAND ALL OF THE IMPLICATIONS.

$SCO: will reply with “AOK;” if the command was processed successfully. However, to assure the changes are stored and used the regulator must be reset using the $RBT: command after all changes have been made.

$SCO: will no longer be recognized once it has been locked-out. See section “Restore to As-Compiled (default) Status”

Example: Configure to override DIP switches and positively define system voltage and battery capacity:

- Use CPE#3 (FLA#2 – large batteries)
- 1500AH battery (BC Index = 3)
- 12v system (SV Override = 1)
- Lockout NOT enabled (Allows continued changes)

$SCO:3,3,1,0@
$RBT:@

$SCR: RESTORES System Configuration table to default
Restores system configuration values to original as-compiled (default).

$SCR: will reply with “AOK;” if the command was processed successfully. However, to assure the changes are stored and used the regulator must be reset using the $RBT: command after all changes have been made.

$SCR: will not be recognized if system has been locked-out via the $SCO: command.

$MSR: RESTORE all parameters (to as defined at program compile time
Restores all configurable parameters to the as-compiled (default) values. This is a combination of the $SCR: , $CCR commands, the $CPR:n commands for all charge profile entry (CPE) tables, and $RBT; command. Plus, any calibrations done are cleared. It performs the same function as holding Feature-In restore function (Refer to the Reference Manual “RESTORE TO ASCOMPILED (DEFAULT) STATUS” ). Alternator will RESET after this command is completed.

$MSR:

Note $MSR is disabled if the regulator has been locked out via the $SCO command. In this case, you will need to do to do a full system reset via the Feature_in connector or re=flash the firmware. If successful, the regulator will reply with “AOK;” and then reboot.

$MSR: will not be recognized if system has been locked-out via the $SCO: command.

$EDB: Enable DeBug serial strings

Will cause regulator to start sending $DBG; strings via ASCII Serial USB communication port. This has the like effect to adding “#define DEBUG” to the source code, except $EDB: will ONLY enable the serial strings. Other debug features will not be changed. This command is also only effective for the time the regulator is running. If it is powered down, or reset (for example by a fault, or by receiving a command string that causes a reset), the regulator will restore to its default handling of $DBG: strings. See Appendix G for details on the output of the debug string returned in response to the $EDB: request.

$EDB:

$RBT: ReBooT system
Will cause regulator to reset. This is useful to load any changes from saved Flash memory into the regulator for its use.

$RBT:

$RBT: will not be recognized if system has been locked-out via the $SCO: command.

It is strongly suggested that you use the $RBT command after you have finished making changes to the alternator’s configuration via other ASCII commands. This will restart the regulators, allowing those changes to be recognized – but more importantly, some hardware needs the $RBT: command as a signal to actually save requested changes in non-volatile memory.

$FRM: Force Regulator Mode
This command (with its parameters) will force the regulator to change its current mode to the one indicated. Once forced into a mode the regulator will continue to manage the system accordingly, even if this means the regulator immediately exits the forced mode. For example, if you force the regulator into float mode, but the amps being taken from the battery exceed the exit_float criteria, the regulator will return to the bulk phase.

$FRM:<Mode>

Mode: <Character> The ASCII character immediately following the ‘:’ will be used to force the alternator mode. Character must match EXACTLY the following (including case), must be IMMEDIATELY after the ‘:’, but may be followed by any number of additional characters.

B | = Force into BULK mode.
A | = Force into ACCEPTANCE mode.
O | = Force into OVER-CHARGE mode.
F | = Force into FLOAT mode.
P | = Force into POST-FLOAT mode.
E | = Force into EQUALIZE mode.

Any other character will be ignored and no change will be made. If the active Charge Profile has ‘disabled’ a given phase, the regulator will immediately exit that phase – even if it is ‘forced’ into it, and switch to the next appropriate phase. Also note that if the exit criteria of a forced-mode phase is met, the regulator will again exit that phase quickly.
In such cases the mode may be changed before the next $AST string is sent.

Examples:
$FRM:B | → Forces regulator into BULK mode
$FRM:Bulk | → Forces regulator into BULK mode
$FRM:Bob@ | → Forces regulator into BULK mode (Note use of ‘@’ as needed with Arduino IDE terminal)
$FRM:b | → Ignored (lower case ‘b’)

No pre-existing condition check is made when receiving these mode change commands. For example, normally you would be able to enter equalize mode only if the regulator was already in float or post-float mode. However, the $FRM: command can force the regulator into equalize mode directly from any state, including bulk or ramping. (Do remember: as noted above - if conditions are such, it may not stay in equalize very long.)

35

## APPENDIX D: DETAILS OF CPE (CHARGE PROFILE ENTRIES)

The following are excerpt from the CPE.H source code file to give more details on how each parameter impacts battery charging.

//----- This structure defines a 'profile' for battery charging. | Each stage consist of 'modes', primarily: | Bulk, Acceptance,
// | Overcharge, and Float. | Each mode has a max voltage set point, and criteria for exiting that phase (Exceeding a time limit,
// | or Amps dropping below a given value). | Of special note is the entry Float and Post Float, which have additional criteria
// | resuming charging.
//
#define MAX_CPES 8 | // | There are 8 different Charge profile Entries

#define CUSTOM_CPES 2 // | The last two of which are set aside as 'customizable' and are changeable via the ASCII string commands.

// create human-readable names for charge profiles
// *** BE CERTAIN THESE CORRESPOND TO ANY CHANGES MADE IN CPE.cpp ***
enum ChargeProfiles {LIFELINE, STD_FLA, HD_FLA, AGM_2, GEL, FIREFLY, FOUR_STAGE_FLA, LIFEPO4};

typedef struct
{ // Charging Profile Structure
const char *BATTERY_TYPE; | // String for the battery type
float ACPT_BAT_V_SETPOINT; | // Set point for Ramp, Bulk and Acceptance battery voltage.
// Alternator will transition from BULK mode into Accept Mode when this voltage is reached, // and then start the Accept Duration counter.

uint32_t EXIT_ACPT_DURATION; // Stay in Accept mode no longer then duration in mS
//(Set = 0 to disable Acceptance phase and move directly to OC or Float mode)
int EXIT_ACPT_AMPS; | // If Amps being delivered falls to this level or below, exit Accept mode and go to next
// | Set ExitAcptAmps = | 0 to disable Amps based transition and only rely on EXIT_ACPT_DURATION
timeout.
// | Set ExitAcptAmps = -1 to disable Amps based transition and rely on EXIT_ACPT_DURATION timeout
// | or ADPT_ACPT_TIME_FACTOR adaptive duration.
// | Set ExitAcptAmps = Same value used for LIMIT_OC_AMPS if Overcharge mode is to be used.
// Note: | If both Time and Amps are set = 0, Acceptance will be bypassed.
// FUTURE: | EXIT_ACPT_DVDT | Add dV/dt exit criteria for Acceptance mode, need to decide what it is :-)

// Overcharge mode is sometimes used with AGM batteries and occurs between Acceptance and Float phase.
int LIMIT_OC_AMPS; | // During Overcharge phase, Amps are capped at this low value. | (Set this = 0 to disable OC mode.)
float EXIT_OC_VOLTS; | // Overcharge will continue until the battery voltage reaches this level.
uint32_t EXIT_OC_DURATION; // Over Charge mode duration in mS.
// ( as a safety step, setting OC_VOLTS or DURATION = 0 will also disable OC mode..)
// FUTURE: | EXIT_OC_DVDT | Add dV/dt exit criteria for Overcharge mode, need to decide what it is :-)
float FLOAT_BAT_V_SETPOINT; | // Set point for Float battery voltage, do not exceed this voltage.
int LIMIT_FLOAT_AMPS; | // During Float, manage system to keep Amps into Battery at or under this value.

36

// May = 0, set = -1 to disable limit.
uint32_t EXIT_FLOAT_DURATION; // Alternator will stay in Float mode this int32_t (in mS) before entering Post-Float (no charging)
// | mode. | Set = 0UL disable transition to Post-float mode.
int FLOAT_TO_BULK_AMPS; | // If Amps being delivered exceeds this value, we will assume a LARGE load has been placed on the
battery and we need to re-enter
// BULK phase. | Set this = 0 to disable re-entering BULK phase feature
int FLOAT_TO_BULK_AHS; | // If the number of Ahs removed from the battery after 1st entering Float mode exceed this value, revert
back to BULK.
// Note this will ONLY be usable if the Amp shunt is at the battery. | Set = 0 to disable this feature.
float FLOAT_TO_BULK_VOLTS; | // As with Amps, if the voltage drops below this threshold we will revert to Bulk. | Set = 0 to disable.

uint32_t EXIT_PF_DURATION; // Only stay in Post_float mode (no charging) this amount of time.
// | Set = 0UL to disable times based Post-float exiting and exit only on Voltage.
float PF_TO_BULK_VOLTS; | // If during Post-Float mode VBat drops below this voltage, re-enter FLOAT mode.
// Set = 0.0 to disable exiting of post-float mode based on voltage.
// Config note: | IF you configure the system to enter post-float mode from float-mode
// | (by setting a time value EXIT_FLOAT_DURATION), AND you
// set both EXIT_PT_DURATION and PF_TO_BULK_VOLTS = 0,
// the regulator will in effect turn off the alternator once charging is completed
// | and not restart a charge cycle until powered down and up again.
// | This can be useful if you truly want a one-time only charge.
//You could also config the FEATURE-OUT port to indicate the complete charge cycle has finished,
// | to say power-off the driving engine
int PF_TO_BULK_AHS; | // If the number of Ahs removed from the battery after 1st entering Post Float mode exceed this value,
revert back to BULK.
// Note this will ONLY be usable if the Amp shunt is at the battery.
// | Set = 0 to disable this feature.
float EQUAL_BAT_V_SETPOINT; | // If Equalize mode is selected, this is the target voltage. | Set = 0 to prevent user from entering
Equalization mode.
int LIMIT_EQUAL_AMPS; | // During equalization, system will limit Amps to this value.
//Set = 0 to disable amp limits during Equalization Mode. uint32_t EXIT_EQUAL_DURATION; // Regulator will not stay in Equalization any longer then this (in mS). If set = 0, then Equalization mode will be disabled.
int EXIT_EQUAL_AMPS; | // If Amps fall below this value during Equalization while at VBat setpoint -- exit equalization.
// | Set = 0 to disable exit by Amps and use only time.
float BAT_TEMP_1C_COMP; | // Battery Temperature is compensated by this factor for every 1C temp change.
// | Note this is based off of BAT_TEMP_NOMINAL (25c)
int MIN_TEMP_COMP_LIMIT; // If battery temperature falls below this value (in deg-c), limit temp compensation voltage // rise to prevent overvoltage in very very cold places. int BAT_MIN_CHARGE_TEMP; // If Battery is below this temp (in deg-c), stop charging and force into Float Mode to protect
// | it from under-temperature damage.
int BAT_MAX_CHARGE_TEMP; // If Battery exceeds this temp (in deg-c), | stop charging and force into Float Mode to protect
// | it from over-temperature damage.
uint8_t CPSPLACEHOLDER[8]; // Room for future expansion
} tCPS;

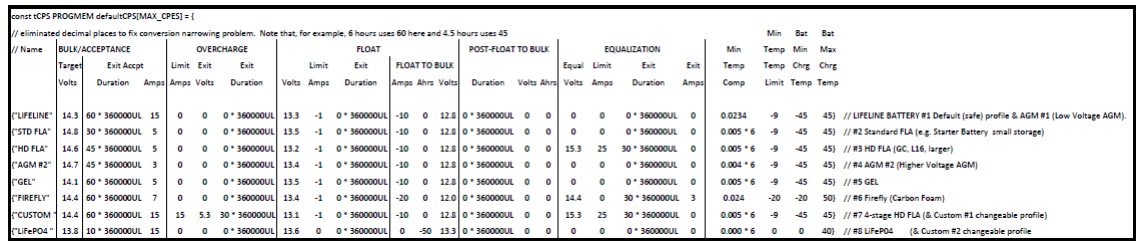
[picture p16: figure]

37

#define BAT_TEMP_NOMINAL 25 | // Nominal temp which .BAT_TEMP_1C_COMP is based around (in deg-C).

#define PID_VOLTAGE_SENS 0.020 // When looking at charger mode transitions, if we come within 20mV of the target voltage (for rep 12v battery), consider we have 'met' that voltage condtion.

// | (This is to help with smaller charging sources driving a LARGE battery, where the charging source
// | is not really able to push VBat slightly over the limit..)
Actual content of the CPE tables. | Remember, all references are against a ‘normalized’ 12-volt / 500Ah battery.

38

## APPENDIX E: DEFAULT SYSTEM CONFIGURATION

The following documents default “system” values (as compiled) for the VSMMAR’s system configuration. It is configured assuming both and alternator and battery shunts are installed. Note that a 300A / 75mV shunt is being used on the alternator and a 500A / 50mV shunt is being used on the battery. (The latter is the shunt used in the Link-10 battery meter as well as others).

Settings in System.cpp:

tSCS systemConfig = {
false, // .REVERSED_BAT_SHUNT | --> Assume shunt is not reversed.
false, // .REVERSED_ALT_SHUNT | --> Assume shunt is not reversed.
90, | // .ALT_TEMP_SETPOINT | --> Default Alternator temp - 90c (Approx 195f)
1.00, // .ALT_AMP_DERATE_NORMAL | --> Normal cap Alternator at 100% of demonstrated max Amp capability,
0.75, // .ALT_AMP_DERATE_SMALL_MODE | --> Unless user has selected Small Alt Mode via DIP switch, then do 75% of its
capability
0.50, // .ALT_AMP_DERATE_HALF_POWER | --> User has shorted out the Alternator Temp NTC probe, indicating they want
// | to do 1/2 power mode.
-1, | // .ALT_PULLBACK_FACTOR | --> Used to pull-back Field Drive as we move towards Idle.
0, | // .ALT_IDLE_RPM | --> Used to pull-back Field Drive as we move towards idle.
// | Set = 0 causes RPMs to be determined automatically during operation.
//!! NOTE THAT I SET THIS TO 125 AMPS instead of 0 for my genset
125, | // .ALT_AMPS_LIMIT --> The regulator may OPTIONALLY be configured to limit the size of the alternator output
// | Set = 0 to disable Amps capping.
// | Set = -1 to auto-size Alternator during Ramp. (required Shunt on Alt, not Bat)
0, | // .ALT_WATTS_LIMIT --> The regulator may OPTIONALLY be configured to limit the load placed on the engine via the
Alternator.
// | Set = 0 to disable, -1 to use auto-calc based on Alternator size. (Required Shunt on Alt)
12, | // .ALTERNATOR_POLES | --> # of poles on alternator (Leece Neville 4800/4900 series are 12 pole alts)
((6.7 / 2.8) * 1.00), | // .ENGINE_ALT_DRIVE_RATIO | --> Engine pulley diameter / alternator diameter & fine tuning
calibration ratio
(int)((500 / 0.050) * 1.00), // .BAT_AMP_SHUNT_RATIO **Spec of amp shunt, 500A / 50mV shunt (Link10 default) and % calibrating error
// | CAUTION: Do NOT exceed 80mV on the AMP Shunt input
(int)((300 / 0.075) * 1.00), // .ALT_AMP_SHUNT_RATIO -->
// | DUBLER 061720 CHANGED TO 300A/75mV for alternator shunt

39

// | CAUTION: Do NOT exceed 80mV on the AMP Shunt input

-1, // .FIELD_TACH_PWM --> If user has selected Tach Mode, use this for MIN Field PWM.
// | | Set = -1 to 'auto determine' the this value during RAMP phase
// | | Set = 0 to in effect 'disable' tach mode, independent of the DIP switch.
0, // .FORCED_TM | --> User can FORCE tach mode independent of DIP switch using $SCT command.
// | | 0=DIP/off, 1=Force-on
0, | // .CP_INDEX_OVERRIDE --> Use the DIP switch selected indexes
0.0, // .BC_MULT_OVERRIDE | --> Use the DIP switch selected multiplier
0.0, // .SV_OVERRIDE | --> Enable Auto System voltage detection
0, | // .CONFIG_LOCKOUT | --> No lockouts at this time.
#ifdef BENCHTEST

2, // .ENGINE_WARMUP_DURATION **Shortened for bench testing**
#else

15, // .ENGINE_WARMUP_DURATION --> Allow engine X seconds to start and 'warm up' before placing a load on it.
// | | DUBLER MOD 080320 changed from 60
#endif

0}; // .REQURED_SENSORS --> Force check and fault if some sensors are not present (eg alt temp sensor)

40

## APPENDIX F: ERROR CODES AND MEANING

The following is a description of error codes as reported via the ASCII status and/or the LED blinking pattern. Most errors are hard-faults, indicating a condition which the VSMMAR is unable to decipher or correct itself and as such will shut down until corrected, in order to prevent any potential systems or battery damage. A few errors will attempt to auto-restart to see if the failing condition clears (for example, error low battery voltage).

These error codes may change and be expanded, refer to System.h for latest list. Many error codes are related to internal logic checks, if those are received look for a firmware upgrade. However, some errors codes occur during installation errors and / or system issues. A prime example is the Alternator overheating errors – which typically indicate a need to either increase cooling and/or enable SMALL-ALT-MODE or increase its pullback. These alternator overheating issues are very common when using small frame alternators (anything under 30lbs) combined with large battery banks or any Li-based battery bank.

FET over temperature (error #40) is an indication of a hardware issue with the regulator its self, or perhaps a short in the alternator field.

//---- | Error codes. If there is a FAULTED status, the variable errorCode will contain one of these...
// | Note at this time, only one error code is retained. | Multi-faults will only show the last one in the checking tree.
// | Errors with + 0x8000 on them will cause the regulator to re-start, others will freeze the regulator.
// | (Note combinations like 10, and 11 are not used. | Because one cannot flash out 0's, and kind of hard to
// | tell if 11 is a 1+1, or a real slow 2+0)
#define FC_LOOP_BAT_TEMP | 12 | // Battery temp exceeded limit

#define FC_LOOP_BAT_VOLTS | 13 | // Battery Volts exceeded upper limit (measured via INA226)

#define FC_LOOP_BAT_LOWV | 14 | + 0x8000U | // Battery Volts exceeded lower limit, either damaged or sensing wire missing.

// | (or engine not started!)
#define FC_LOOP_ALT_RPMs | 22 | // Alternator seems to be spinning way to fast!

#define FC_LOOP_ALT_TEMP_RAMP | 24 | // Alternator temp reached / exceeded while ramping - this can NOT be right,

// | to reach target while ramping means way too risky.
#define FC_LOG_ALT_STATE | 31 | // Global Variable chargingState has some unsupported value in check_for_faults()

#define FC_LOG_ALT_STATE1 | 32 | // Global Variable chargingState has some unsupported value in | manage_ALT()

#define FC_LOG_CPI_STATE | 33 | // Global Variable cpIndex has some unsupported value in caculate_ALT_Targets()

#define FC_LOG_CPINDEX | 34 | // Global Variable cpIndex has some unsupported value in check_for_faults()

#define FC_LOG_SYSAMPMULT | 35 | // Global Variable systemAmpMult has some unsupported value in check_for_faults()

#define FC_LOG_BAT_STATE1 | 36 | // Global Variable chargingState has some unsupported value in manage_BAT()

#define FC_SYS_FET_TEMP | 41 | // Internal Field FET temperature exceed limit.

#define FC_SYS_REQIRED_SENSOR | 42 | // A 'Required' sensor is missing, and we are configured to FAULT out.

#define FC_ADC_READ_ERROR | 71 | // Internal error - unable to use ADC subsystem

#define FC_BAT_INA226_READ_ERROR | 100 + 0x8000U | // Returned I2C error code is added to this, see I2C lib for error codes.

#define FC_ALT_INA226_READ_ERROR | 200 + 0x8000U | // Returned I2C error code is added to this, see I2C lib for error codes.

## APPENDIX G: Debug String Contents

The $EDB: request will return the following data:

Timestamp in to the 1/1000 of a second Charging State
fieldPWMvalue,

Feature-in port 1 state
Feature-in port 2 state
Feature-in port 3 state

PWMErrorV, PWMErrorA, PWMErrorW, PWMErrorAT, PWMError,

errorAT,

'B' followed by
measuredBatVolts to three decimal places measuredBatAmps to one decimal place

'A' followed by
measuredAltVolts to three decimal places measuredAltAmps to one decimal place

thresholdPWMvalue
fieldPWMLimit,
otPullbackFactor to two decimal places

measuredAltTemp, measuredBatTemp, in degrees C

the results of checkStampStack() which reflect how much of the stack has been used

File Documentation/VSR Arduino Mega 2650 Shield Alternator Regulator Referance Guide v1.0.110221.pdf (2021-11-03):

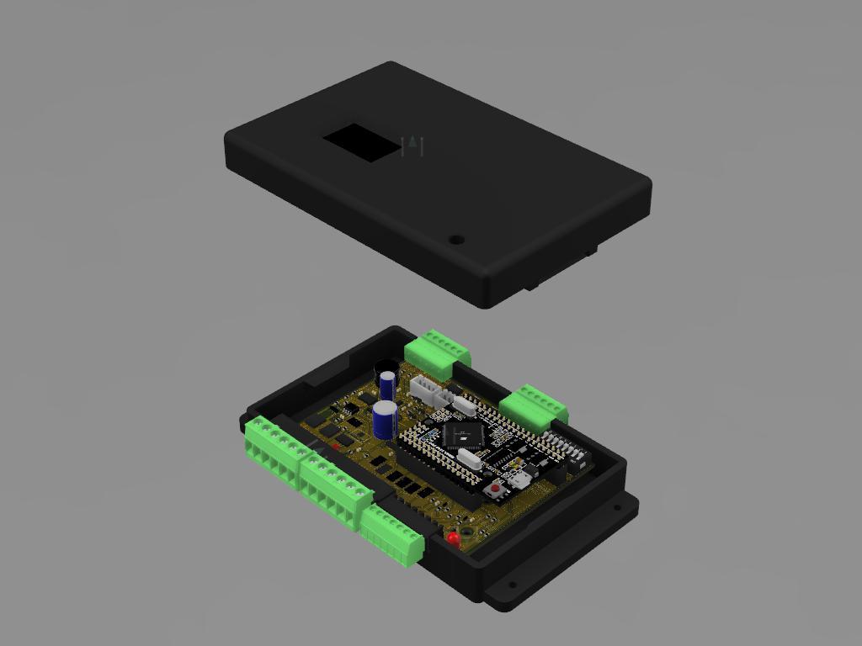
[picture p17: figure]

i

# ALTERNATOR REGULATOR VSR Mini Mega 2650

# With optional remote TFT LCD display

AN OPEN-SOURCE INTELLIGENT ALTERNATOR REGULATOR - Redesigned

# Reference Manual

### https://github.com/peteDDD/VSR-Mini-Mega-Alternator-Regulator

Rev 11/1/2021 – Work in Process.

Adopted from the outstanding work of William A. Thomason on several generations of VSR Alternator Regulators

Original work Copyright 2018 – William A. Thomason

Derived work Copyright 2020/2021 – Peter Dubler

Released Under Creative Commons Attribution-Noncommercial-Share Alike 3.0 http://creativecommons.org/licenses/by-nc-sa/3.0/

i

## ACKNOWLEDGMENTS

The source code and hardware described here are derived directly from the tireless work of William “Al” Thomason on several generations of Arduino-based alternator regulators.

Al’s work took a core of software forward over several hardware sets. The software carried forward support of all of that hardware though extensive #ifdef and #define statements as well as a portability.h file and other code considerations. This derivative attempts refactor that code to a new hardware base, with no support of other hardware, thus attempting to simplify the new code base while adding additional features and extensibility for future expansions.

At the real core of this alternator controller’s functionality is Al’s PID control software. That code is left, somewhat as a shrine of engineering exceptionalism, untouched.

There were many artifacts of the long history of the original code remaining in the original code from the many generations of functionality and different boards developed by Al. It was my objective to remove thet unused code carefully so as to not damage any data structures with unanticipated effects.

## TABLE OF CONTENTS

## THE VSR MINI MEGA ALTERNATOR REGULATOR: OVERVIEW

What the heck does “VSR” mean? Not entirely sure but one possibility is “Voltage Sensitive Regulator” is a possibility. Sure, this regulator senses voltage from the alternator and the battery but that is just a small part of the full regulation and functionality story of which you will read more about below. “Voltage Sensing Relay” is another possibility. A VSR in that context can be used to connect a starter battery bank and house battery bank together once one exceeds a set voltage such that one bank cannot draw down the other when cross charging. Yes, this regulator can also provide that function with the addition of an external relay or contactor. But that too is not all…

“House Batteries” are common on RVs, boats, remote cabin / houses. These battery banks often represent investments in the hundreds if not thousands of dollars, so it is well worth the effort to take care of them.

The use of an external alternator regulator is a well-known way to improve over standard ‘auto’ internal regulators. With accurate measurement of battery voltage, and then control of the alternators field to adjust its output, these often provide several important features such as soft starting to save wear on belts, multi-stage charging to assure faster and more complete recharging, and temperature sampling of the battery to precisely adjust target voltages. But with almost universal exception, almost all currently available external chargers are lacking one key ability: the ability to monitor current as well as voltage.

Sampling the specific gravity of the battery acid is often the preferred way to determine the true SOC of a battery. Another approach recommended by many battery manufacturers is to monitor the amount of current a battery is accepting¹ while recharging. By continuing to hold a battery in the acceptance phase until these manufacturer’s recommended thresholds are meet, we can assure a battery is indeed fully recharged. Without the ability to measure current, most common regulators revert to another approach for determining if a battery is fully recharged: they guess.

The VSR Mini Mega Alternator Regulator (“VSMMAR”), as did the many generations of VSR Alternator Regulators (“VSRAR”), includes the ability to monitor current in addition to voltage and temperatures. It also provides the ability to limit alternator output to protect the alternator, battery and/or engine (depending on how it is configured). The Mini Mega version has support for 12V and 24V systems, whereas the earlier VSR versions also supported 48V systems. The Shield version drops support of the relatively rare N-type alternators in favor of simplicity and only supports P-type alternators.

The VSMMAR may be used in many applications but understanding the design focus provides some insight into the feature choices (both additions and subtractions) as compared to the VSRAR. The design focus of the VSMMAR has been, without in any way reducing its optimization for larger engines, to support a 6-HP diesel DC genset sporting a 200-amp large-frame alternator and a SCUBA compressor engaged by an electric clutch. This focus intends to maintain maximum output of the alternator by directly measuring amps generated at a level that does not bog down the engine. A feature-in port option allows the switch which engages the SCUBA compressor clutch to signal the VSMMAR to reduce the alternator field signal and thus the alternator’s engine load to a pre-designated level, leaving the rest of the engine horsepower available for the SCUBA compressor.

1 Example, see: “Exide Battery Charging & Storage Guidelines 5_9_13” --www.exide.com/Media/files/Downloads/TransAmer/Battery Care and Maintenance/Battery Charging & Storage Guidelines 05_9_13.pdf

The VSMMAR, as compared to the VSRAR, adds a second INA226 to measure voltage and current. As such, the
VSMMAR directly supports and is intended to be used with two amp shunts, one at the alternator and one at the battery bank for maximum benefit. The VSMMAR software can be configured for only one shunt as well.

The VSMMAR has three feature-in and three feature-out ports, whereas the VSRAR had only one of each. These ports can be activated to each perform a variety of features and feature-in or feature-out functionality can be assigned to any of the feature-in or feature-out (respectively) ports. The feature-in and feature-out ports can each be assigned to a variety of optional functions. These options and the assignment of the ports is easily accomplished in the Config.h header file where #defines are uncommented to activate the functionality or edited to select the port number. Feature-out functionality in the code includes: echoing of the red and green on-board LEDs to feature-out ports, mimicking an old-fashioned “alternator lamp” on a feature-out port, providing an engine stop pulse, providing a LiFePO4 BMS alarm, and/or providing a battery combiner signal to tie starter and house battery banks together while the alternator is actively charging. Feature-in function options include the previously mentioned “SCUBA” compressor input, an input to initiate battery equalization, an input, which, in combination with dipswitch setting, resets the system to the “factory” settings, and a disable (aka “force-to-float”) input which keeps the charging state in float charging mode.

The VSMMAR also adds headers for two separate serial ports, which do not interfere with the serial port used by the USB for programming of the Arduino Mini Mega processor board. Of the two serial ports, either one can be used to optionally support a remote TFT LCD display which displays all of the same data which the OLED can plus any fault codes encountered and a historical graph of voltage and (alternator) current over the current charge cycle. This display uses an Arduino Uno with a TFT LCD shield. (A bezel for panel mounting this display has also been designed for 3-D printing. The materials for this display may be found in the github for this project. The second serial port, could be used to monitor a LiFePO4 battery management system to detect impending shutdown events and to turn of the PWM output of the regulator before the battery is disconnected by the BMS, thus protecting the alternator from being fried by a voltage dump. Presently there is a stub in the firmware to support this function and it will be coded in the near future. This port could be used for any other function the user might care to code. For example it could be used to provide NMEA-0183 output with addition programing.

There are also two I2C/5V/GND 4-pin headers on the VSMMAR. One can be used for adding a small SSD1306-based OLED to display dynamic data. As coded, when this option is enabled the following can be/is displayed on the OLE: boot-time information including software rev, battery type, battery bank size, small alternator mode, and tach output mode. After boot, the following is displayed on the OLED: battery and alternator voltage, amps, and temperature, field PWM, charging state (in words, not as a number), countdown of time remaining in warm-up and ramp-up phases, time in current charging state, error messages, and a flag for indicating that the SCUBA compressor is engaged, if that feature is enabled.

During installation, an amp shunt is placed on the house battery to monitor current into and out of the battery. You may already have such a shunt already installed, for example if you use a battery monitor along the lines of the Link-10. In this case, simply reuse the same amp shunt, though do make sure the regulator is correctly configured to match the shunt properties (typically stamped on the shunt but also can be derived by measuring the resistance of the disconnected shunt and doing the math) (the default shunt value expected for the VSMMAR is 300A / 75mV, i.e. 200A / 50mV).

Another way to utilize the alternator regulator is to place the amp shunt on the alternator, as opposed to, or in conjunction with, locating one at the battery. With this configuration, the amps monitored can more closely focus on the alternator and one is able to configure the VSMMAR to limit the amount of amps produced, and hence the load the alternator places on the engine. This can be VERY IMPORTANT when switching from traditional batteries to LiFePO4 batteries and the ability of LiFePO4 batteries to accept high charging currents could easily exceed the alternator’s design capabilities. This can also be useful in cases of building a DC generator where the alternator is much larger than the engine is able to support. By capping the amount of power the alternator is allowed to produce, you can match its demands to the capability of the engine. A shunt on each the battery and the alternator provides the most rapid charging of the batteries as it considers both the output of the alternator as well as the current actually flowing to the batteries. The VSMMAR was designed to have the user implement two shunts without having to add any other hardware.

Although it would be a waste of hardware and software, the VSMMAR may also be used in conventional voltage-only mode² by simply not connecting the Amp Shunt (place a small wire across the Amp Shunt terminals to remove the chance of any electrical noise fooling the regulator). The Regulator will fall back to time-only charge profiles, though with very accurate measurement of voltages. In addition, acceptance phase will utilize an ‘adaptive’ time-based formula; it will remain in acceptance phase for 5x the duration the regulator was in bulk mode, or the configured maximum amount of time contained in the CPE (charging profile) – whichever is less. In this way, the battery gains more protection from over charging when the regulator is unable to measure the amps.

### WHAT IS A “SYSTEMS-BASED APPROACH”?

Even the most basic DC battery and an associated charger is a `system’, it is only a question of how well the system works. Voltage-only regulators have only one channel of communications: voltage. Though very important, it leaves no ability to communicate any other information, hence the addition of additional sensors: temperature probes, current shunts, etc. But even with added sensors there is still only one channel of communications: voltage. And having only one channel of communication can be restrictive and starts to introduce compromises.

The 3

rd generation of the VSR Alternator Regulator added a CAN (Control Area Network) port to provide for a robust proven communications path between devices connected to and surrounding the battery. It attempts to provide the most extensive systems control however its promise has yet to be realized since low-cost CAN battery monitors and coordinating solar and wind charging controllers are not yet available commercially or from the open-source ecosystem. For more on this, refer to the VSRAR manuals.

Lacking economical CAN-based accessories, and adding a second INA226 to the VSMMAR, CAN was not included on the VSMMAR. If CAN functionality is critical to your implementation, consider the WS500 commercial product or consider coding your own CAN drivers into the VSMMAR, perhaps leveraging the VSRAR open-source code which included such functionality.

2
Voltage-only mode is detected when the alternator regulator is unable to measure current in excess of +5A at any point in time. Under this case the code will ASSUME the amp shunt is either not connected, or damaged and will fall back to time-only exit criteria. (i.e., all the charge profile (CPE) values will be assumed set = 0 (disabled). See source code “#define USE_AMPS_THRESHOLD” to control this capability.

### CONNECTIONS

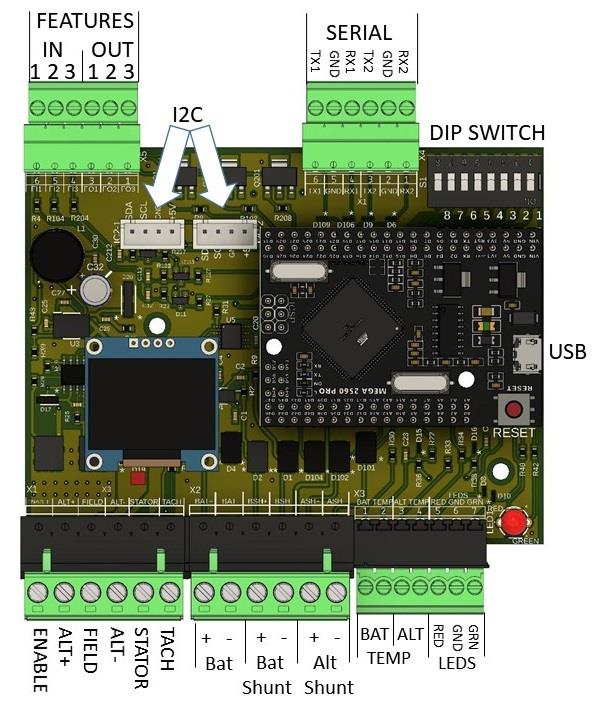
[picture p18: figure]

Figure 1: Board Connections

ENABLE | Connect to VBat+ to ‘turn on’ the regulator. This could be the key switch of an engine or switched through an oil pressure switch on an engine. Use min 14AWG wire and a 2A fuse.
ALT+ | Connect to + (Bat) terminal of Alternator. Use wire sized to match your expected maximum Field current draw and protected by an appropriate fuse. (typically 4-12A, depending on alternator size) (Min 14AWG – use 12AWG or 10AWG for large frame alternators)
FIELD | Connect to the field of the alternator. VSMMAR supports only the common P-type alternator field input. Use wire of sufficient gauge to carry the expected current, up to 32A (connector limit) (Min 14AWG).
ALT- | Connect to the – (gnd) terminal of Alternator using appropriate wire. (Min 14g)
STATOR | (optional) Connect to an Alternator Stator pole via 2A fuse and 16AWG wire. Used to increase battery voltage measurement accuracy, as well as enable several battery and alternator protection features in the regulator.
TACH | (optional) Output to drive a tachometer when TachMode is enabled. Requires Stator input
BAT+ | Connect directly to the battery via 14AWG wire protected with a 2A fuse located at the battery. (Do not connect after any busses, shunts, etc.)
BAT- | Connect directly to the battery via 14AWG wire protected with a 2A fuse located at the battery. (Do not connect after any busses, shunts, etc.)

BAT
SHUNT
+/-

ALT
SHUNT
+/-

(technically optional but highly recommended) Connect to current shunts using twisted pair 16AWG or larger wire. The current shunt maybe installed in either a ground wire (low shunt), or in the + voltage wire (high shunt). Do not exceed 80mV difference between + and - inputs, nor exceed connect to a shunt more than 32v above ground. If the current shunts are not being used, it is suggested to place a wire between these two terminals to avoid any electrical noise confusing the regulator. “+” and “-“ refer to the higher and lower voltage side of each shunt. For example, if the shunt is on the positive terminal of the alternator, the “+” side of the shunt is the one closest to the alternator.

BAT and ALT TEMP | Connect 10Kohm 3950 beta NTC temperature sensors from battery and alternator. This connections are not polarized. See more on temperature sensors later in this manual.
LEDS Red Gnd Grn | The status and error on-board bi-color LED output is echoed to these pins using two LEDs; red and green. Connect LEDs directly to these terminals. The Gnd terminal is shared between the two LEDs. 22awg or larger wire. These LED could for example be added to the engine gauge panel for remote monitoring of the VSMMAR.
FEATURE-IN 1, 2, 3 | See details later in this manual
FEATURE-OUT 1, 2, 3 | See details later in this manual

SERIAL
TX1, GND, RX1
TX2, GND, RX2

See details later in this manual

Figure 2: Connection Table

### CONNECTIONS AND FEATURES ENABLED

The VSMMAR minimal installation needs only 6 wires to be connected (See “Example 1: Minimal (Voltage Only) Installation” on page 21) and will operate as a highly capable multi-step voltage regulator, where charging decisions are based on time. Adding sensing wires unlocks additional features. The following table highlights a few of these capabilities and connections needed.

| Minimal Required Connections BAT+, BAT-, ALT+, ALT, PWM, ENABLE | Additional Connections (can be used individually or in combination)
Highly accurate voltage-based charge regulation | ✓
Battery temperature compensation | | ✓
Alternator overheating protection | | | ✓
Battery measurement-based charging | | | | ✓

Figure 3: Features enabled by connections (Capabilities of the VSMMAR. not exhaustive, only illustrates some of the main features)

### WHY DO WE NEED A STATOR WIRE?

The MMAR includes a wire to be connected to one of the stator terminals on your alternator. Though optional, attaching this wire will improve the accuracy of voltage measurements, and enable several protection features.

- Improved voltage measurement by synchronizing the sampling of battery voltage with the stator. This is a ‘best Practice’ for measuring battery voltage as it allows us to see the true ‘high point’ of the alternators output each time we measure battery voltage. It also reduces external noise and other issues versus sampling alternator voltage at random times. Battery voltage is measured to a resolution of 1.25mV (a bit more than 0.001 volt. By using the stator wire we are able to maximize the accuracy of the voltage measurements.
- Connecting the stator wire is also needed to facilitate TachMode.

- Stator Sample also enables a few protection features. For example, if at some time we see some stator pulses, and then they disappear, we assume the engine has stopped. In this condition we reduce the field PWM drive greatly. Without the stator wire we have no idea this has happened (remember, other sources might be charging the same battery, so looking for a drop in VBat is no use). This prevents the regulator from continuing to apply field current and heating up the alternator.

Special note: If your existing installation has additional lamps, resistors, diodes etc. connected to the Stator field, or perhaps a Diode Trio (part of the dash lamp) or ‘exciter’ connection on the alternator, it is advisable to remove these. You can reconnect the dash lamp to one of the feature-out connectors. Leaving existing resistors, diodes, or other connections from the old installation have been known to cause issues with RPM measurements and other features of the VSRAR and presumably will do the same to the VAMMAR.

### WHY DO WE NEED A CURRENT SHUNT?

The VSR Alternator Regulator is fully capable of operating using only battery voltage sensing, and in fact this is a fail-over mode in the case of a missing or broken current sensing probe. In voltage-only mode charging decisions are based on times values, either pre-determined, or at times calculated based on prior phase changes. However, with very few exceptions, battery manufactures preferred charging guidelines call for the monitoring of charge acceptance current as a critical factor in making charger mode decisions, specifically when to end the acceptance phase. As a battery is held in acceptance phase the amount of current being accepted by the battery has a direct correlation to a batteries SOC (state of charge). Monitoring acceptance current allows the regulator to make better decisions and safer charge profiles: using a lower acceptance voltage set point while still allowing for the complete recharging of the battery. LiFeP04 and related battery technologies greatly benefit by this ‘lower stress’ charging approach of a proper acceptance phase vs. being held long enough to assure a fully charged battery, and no more, thus reducing battery stress as a result of overcharging.

Contrast this to time-based decision criteria which uses fixed or perhaps a calculated time basis for determining the batteries needs; perhaps adding a bit of extra time just to make sure. While time-based decisions can be estimated in the lab, they are often confounded by real world imitations. Battery age, temperature, model, and other factors all impact the amount of time needed to properly complete an acceptance phase. Adding extra time may potentially result in a more complete battery SOC recharge, however care must be taken with this approach as some battery are less forgiving to overcharging then others. FLA (Flooded Lead-Acid) batteries might just use more water, while some GEL/AGM and any lithium-based battery technologies could be damaged. The alternative of a short acceptance phase has it own issues: chronic under charging has a very detrimental impact on the lifespan of many battery technologies, not to mentioned the underutilization of the full (and paid for) capacity in the battery bank. Another mitigating approach is to monitor the field drive and use that to help augment charging decisions. However field drive decisions have no idea where the alternator output is actually being consumed and can be tricked to either over or under charge. One example is by simply running a concurrent load while charging. If a washer/dryer is being powered via an inverter, field drive decisions will never see a reduced field drive and can easily overcharge the battery.

### MAXIMUM LIMITATIONS

The following table documents maximum allowed values during the operation. Exceeding any of these values may cause unpredictable operation and/or damage. All voltages are referenced to VBat- unless otherwise noted.

Item | Min | Max | Symbol
VBat+ | | 32 | Volts
Enable | 8.5 | 32 | Volts
Alt or Bat Shunt - | -0.5 | 32 | Volts
Alt or Bat Shunt - | -0.5 | 32 | Volts
Alt or Bat Shunt – to + | -80 | 80 | mVolts
Feature-In | -0.5 | 32 | Volts
| | 32 | Volts
| | 0.5 | Amps
Alt+ | | 32 | Volts
Field (B or C) current | | 32 | Amps

Feature-out

Ambient Temperature | -40 | 100 | Celsius

Figure 4: Maximum Values for Connections

Note: Special care should be noted of the current shunt lower voltage limitations. If a current shunt is located in the ground line of the battery or alternator and there is too small of a ground wire between the shunt and the battery ground terminal. A ground-loop may be created and the voltage limits for the current shunt input could be exceeded. Increasing the size of the ground cable, and/or relocating the amp shunt(s) to the positive side of the alternator or battery are potential solutions. Of course, having too small a ground cable on either the battery or the alternator has other implications. When in doubt, oversize the battery and alternator cables.

ACCESSORIES – PROBES, CASES, SHUNTS, ETC.

To install your regulator you may need some or all of the following. There are many ways to purchase these, and the examples given are only one option.

TEMPERATURE PROBES
The VSMMAR uses NTC temperature probes to optionally monitor battery and/or alternator temperature. The NTC temperature probe is a very common one which is easy to source. There are several sources for NTC probes, do make sure to get ones with these specifications:
- Resistance: 10K Ohms
- Beta: 3950

(Note: It is possible to alter these values (to some extent) by making changes to the Source Code)
Searching Ebay or Amazon for “NTC 10K waterproof 3950” will quickly bring up a wide range of suppliers, with cable lengths from 0.5m to 5m. Aliexpress: https://www.aliexpress.com/item/32800546643.html Be sure to purchase a temperature probe with a metal sensor end (not plastic). The metal sensor end can then be pressed into an 8awg (6mm diameter or 10mm²
) 1/4”, 5/16”, or 3/8” non-insulated ring terminal so it can be easily attached to the battery or alternator. Aliexpress: https://aliexpress.com/item/33057214186.html Heat the terminal to expand it then the probe will slide in easily and fit tightly when it cools.

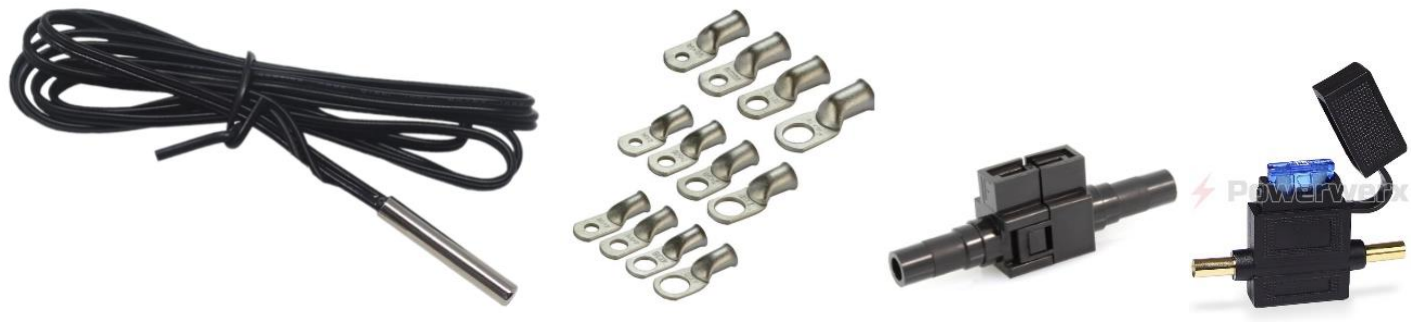
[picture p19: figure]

Littelfuse 01530002H Powerwerz CrimpFuse

ALTERNATOR TEMPERATURE PROBE LOCATION
In most cases the diode pack is the critical limitation in alternators and the best point of reference for measurement, however it is best to consult your alternator manufacturer for recommended placement - as well as for allowable operational limits. Figure 5 below shows the recommended location for the alternator temperature probe from Leece Neville / Prestotolite -- on the diode pack.

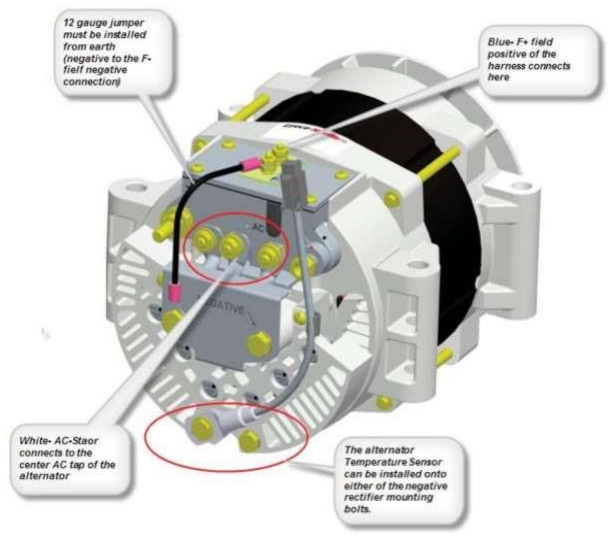
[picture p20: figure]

Figure 5 - Example Alt Temperature probe location

FUSE HOLDERS
It is recommended to install fuses in the locations indicated in the Example Installations. Chose a fuse of appropriate rating (See `Connections’ above) I recommend the Littelfuse 01530002H (https://www.waytekwire.com/item/46036/Littelfuse-01530002H-MINI-Fuse-Holder-/) for wires up to 16awg and 20 amp which uses
mini fuses and is crimped to your wire, making for a very neat installation. For 10 and 12 AWG wire, consider the Powerwerz crimpable ATO fuse holder (https://powerwerx.com/crimpable-inline-atc-blade-fuse-holder) (and some heat shrink tubing). Remember, Fuses are primarily intended to protect wires, not the device – with one exception: the field fuse will also help protect the Alternators Regulators field drive circuit – choose a fuse about 50% higher than you expected maximum field draw. For smaller alternators, a 10A fuse should be sufficient, while larger units may need a 15A fuse. If you are driving multiple alternators in parallel from one VSR Alternator Regulator, adjust the fuse size accordingly, but do not exceed 32A as that is the terminal strips maximum rating.

CURRENT SHUNTS
Many installations already have a battery current shunt installed, often as part of an existing battery meter. If so, simply attach the Current Shunt leads to that existing shunt. The battery shunt may be located in the + or the – wire with no adjustments needed for your regulator. The VSMMAR shunt wires can be placed in parallel with the existing shunt wires. The shunt negative wire should be on the side of the shunt closest to ground and the positive wire, on the side of the shunt furthest from ground or closest to the positive terminal of the battery.

Similarly for the alternator shunt, the negative terminal should be closest to ground and the positive terminal furthest from ground. See Figure 6.

For the wires running to the shunt, twist a pair of 16awg wires using an electric drill. (Pro tip: don’t cut the wire to length until after it is twisted and routed. The pair of wires will be substantially shorter after twisting.) The twisted pair will reduce the likelihood of induced currents causing errant readings.

If the current shunt wires are connected in reverse, the current indicated on the OLED will reflect negative numbers. You can either reverse the wires for the respective current shunt or change the systemConfig.REVERSED.BAT.SHUNT or system.Config.REVERSED>ALT>SHUNT flag(s) in the System.cpp.

By default the regulator is configured for a 300A/75mV shunt (common on many battery monitors). If you are using different shunts, you can either use the $SCA: command to inform the regulator of the shunt values or edit the values in the System.cpp file. For example to change the battery shunt calibration to a 500A/50mV shunt,

(int)((300 / 0.075) * 1.00), // .BAT_AMP_SHUNT_RATIO

Would be changed to:

(int)((500 / 0.050) * 1.00), // .BAT_AMP_SHUNT_RATIO

CAUTION: Do not use a shunt whose voltage exceeds 80mV, or inaccurate results will occur as well as a potential for damage.

Shunts are known for being less than accurate, and if you find the calibration of the VSR Alternator Regulator is off, you may use the $SCA: command to adjust for any error or by editing the System.cpp file as noted above.

ENCLOSURE
A 3-D printable custom case can be found in the github files:

https://github.com/peteDDD/VSR-Mini-Mega-Alternator-Regulator

There are two versions of the lid, one with a hole for the USB connector and one without. There is also a file for a removable plug for the USB connector hole.

WATERPROOFING
It is recommended that the PCBs be sprayed with a silicone conformal coating.

## REGULATOR INSTALLATION OPTIONS

The VSMMAR is a very versatile device with several installation options depending on your goals and objectives. In its simplest form, the Enable, Alt+, Alt- and Field wires are all that need be connect, and in this mode the regulator will behave as many voltage-only regulators, albeit with a high level of precision. Adding additional sensing capabilities will unlock additional capabilities of the VSMMAR.

The following will give an overview of how to connect and configure the regulator in different situations. The recommended dual amp shunt installation is covered first. Next, some “simpler” but less efficient and less ‘feature-rich’ implementations are shown. Finally, some more complex or specific situations are covered.

### REGULATOR PLACEMENT

Place the near the alternator – keeping the Alt+, Alt- and Field wires as short as reasonably practical. Take into consideration ambient temperature as well as any potential for water splashing and consider augmenting the case as needed. The regulator is very efficient and does not need much cooling beyond what is typically found in engine room compartments, but that is not to say one should test its limits!

### CAUTIONARY NOTE: OVERSTRESSING SMALL-FRAME ALTERNATORS

The most common alternator found will be a small frame unit, especially if it is the OEM alternator on an engine. These alternators are good reliable units, but may not be up to the demands of delivering large amounts of current over a long period of time. Overstressing alternators can result in damage from burnt-out diodes and/or internal heat stress-related damage and failures. Such stress conditions are exacerbated by high-acceptance battery banks (eg, Lithium, AGM/GEL, or even large-capacity standard wet-cell FLA batteries).

The best way to protect a small-frame alternator is to install an alternator temperature sensor, ideally located near or on the alternator’s diode pack. This will allow the VSMMAR to monitor the alternator and reduce output as its safe temperature limit is approached. (It is not unknown to see an ‘80A’ alternator restrained to as low as 30A in order to prevent alternator overheating…). In addition, it is recommended to select ‘Small-Alt Mode’ via DIP switch 6 to provide an overall capping of alternator loading. After some run-time experience has been had, you can consider turning off Small-Alt mode and see if the alternator is able to handle your specific installation.

### OTHER IMPORTANT CONSIDERATIONS

DIODE BASED BATTERY ISOLATORS
These are often installed when one alternator is asked to charge two or more batteries. The isolator prevents any loads on one battery from discharging the other battery when the engine is turned off. These present a problem for the VSMMAR, as it is attempting to decide when the battery is full: which battery does it look at? If you have a battery diode battery isolator it is might be better to replace it with an automatic battery switch/combiner (following). However, if you do install the regulator in a system with a diode battery isolator, it is suggested you pick the battery you with to focus on – place the battery amp shunt on that battery, and attach the battery voltage sensing wires to that same battery. The regulator will then control the alternator to meet the needs of that battery. There is a risk of overcharging the 2nd battery, but that risk existed well before installing the VSMMAR.

AUTOMATIC BATTERY COMBINER
Another way to connect a 2nd battery to the main one is to use an automatic battery switch or digital voltage sensing relay (DVSR). (https://www.bepmarine.com/en/p/710-140A/Digital-Voltage-Sensing-Relay-DVSR) These will sense the voltage of both batteries, and when the time is right, connect them together. If you install in a system with one of these, connect the VSMMAR to the primary (largest) battery bank, placing the battery shunt on that main battery and connecting the Battery + and Battery – sensing wires to that battery. The VSMMAR will focus on that main battery and let the automatic battery combiner deal with the needs of the 2nd battery. A couple of notes:
- Make sure to connect the 2nd battery on the alternator side of the battery amp shunt – it is important that the amp shunt only measure the current needs of the battery we are focusing on.
- There is a #define FEATURE_OUT_COMBINER option in the source code that can be enabled to allow a simple external high-current relay or continuous-duty contactor to be used for a battery combiner. See the section on feature-out options.

CROSS-CHARGING DIFFERENT BATTERY TYPES
As LiFePO4 batteries become larger and more affordable, it is very enticing to switch a boat’s house battery bank to LiFePO4 while keeping the engine starter battery an AGM or other type of battery which works well for engine starting. In this case, the two battery types require different charging regimes. In this case it is best to have the VSMMAR focus on the LiFePO4 bank and use a DC to DC charger (https://www.renogy.com/12v-20a-dc-to-dc-on-board-battery-charger/) to maintain the starter battery.

VOLTAGE-SENSING WIRES
Install the battery and alternator voltage-sensing wires (Bat+ and Bat -, Alt+ and Alt-) directly to the battery and alternator respectively (with recommended fuses). Do not attach the wires after a battery switch, dual-alternator diode separator, the battery Amp Shunt, or a common ‘bus bar’. Instead connect directly to the batteries and alternator for best results.

### RECOMMENDED TWO-SHUNT INSTALLATION

To take advantage of all of the best charging features of the VSMMAR, the connections illustrated below should be made. The shunts may be on either the high or low side of the battery and alternator but placing shunts on the negative side is a more widely accepted practice.

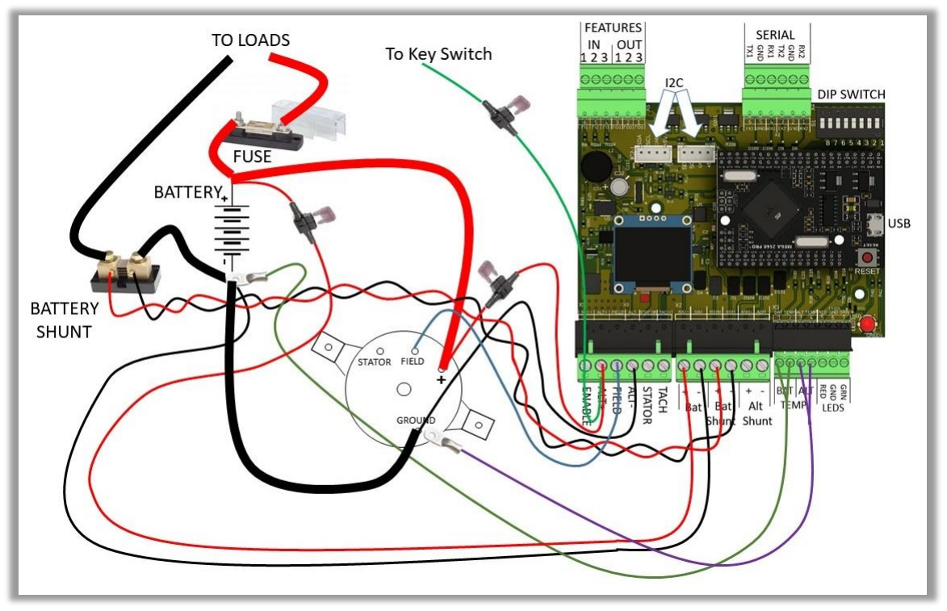
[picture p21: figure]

Figure 6 – Recommended Two-Shunt Installation Connections

### SINGLE-SHUNT INSTALLATIONS: BATTERY-CENTRIC VS. ALTERNATOR-CENTRIC INSTALLATIONS

Throughout the examples it is helpful to keep in mind there are two distinct ways the VSMMAR may be configured and installed in a system, depending on where the amp shunt is placed, if only one shunt is used. If the shunt is placed at the battery the installation is known as a ‘Battery Centric’ installation, allowing for accurately monitor the SOC (state of charge) of the battery and use that to determine when it should change charging phases. (e.g., from acceptance to float).

Though simple to install, it is not suggested to use this configuration as many of the capabilities of the VSMMAR will be disabled. If you do select this installation option take great care with the configuration options (alternator output capping / limitations, CPE selection of voltages and transition times among a few) to best match your typical operations and assure limited risks due to incomplete battery charging and/or alternator overstress situations.

Even with these risks it is helpful to understand this simplest installation as if any of the regulators sensors fail, the VSMMAR will `fallback’ to simpler modes of operation, thereby allowing continued operation, though perhaps in a less efficient manner.

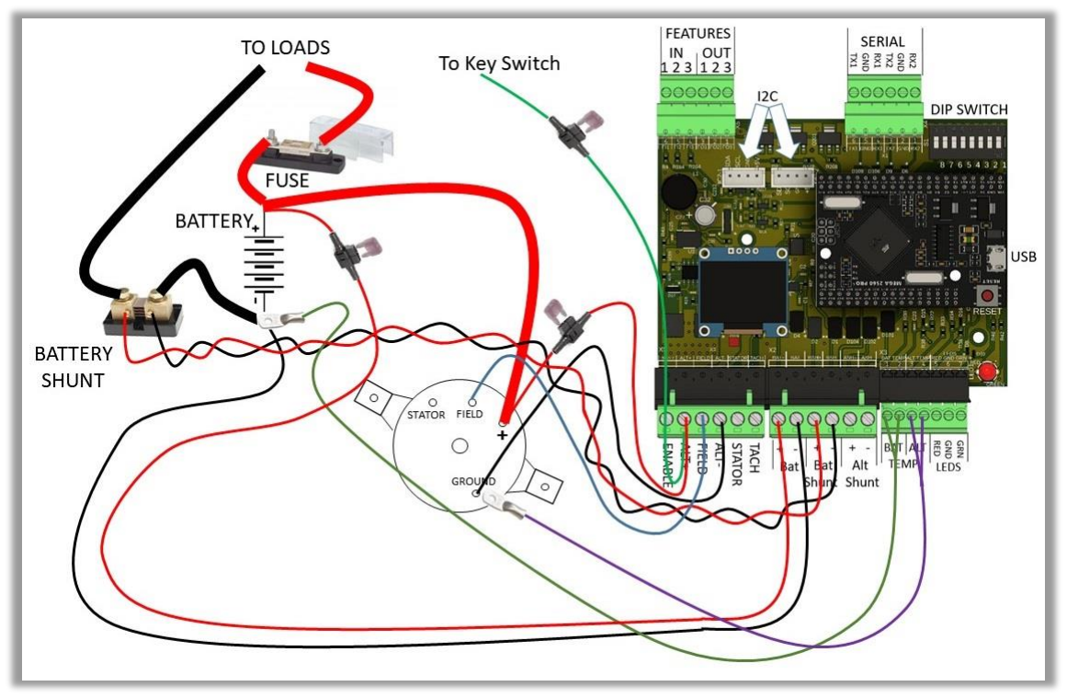
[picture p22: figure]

Figure 7: Battery-centric, Single-shunt Installation

Figure 8: Alternatively, the amp shunt can be placed at the alternator in what is referred to as an ‘alternator-centric’ configuration. This is useful to either further protect a smaller alternator, or perhaps to allow a very large alternator to be placed on a small engine (for example in a DC generator) but this also does not offer the full benefits of a dual-shunt installation.

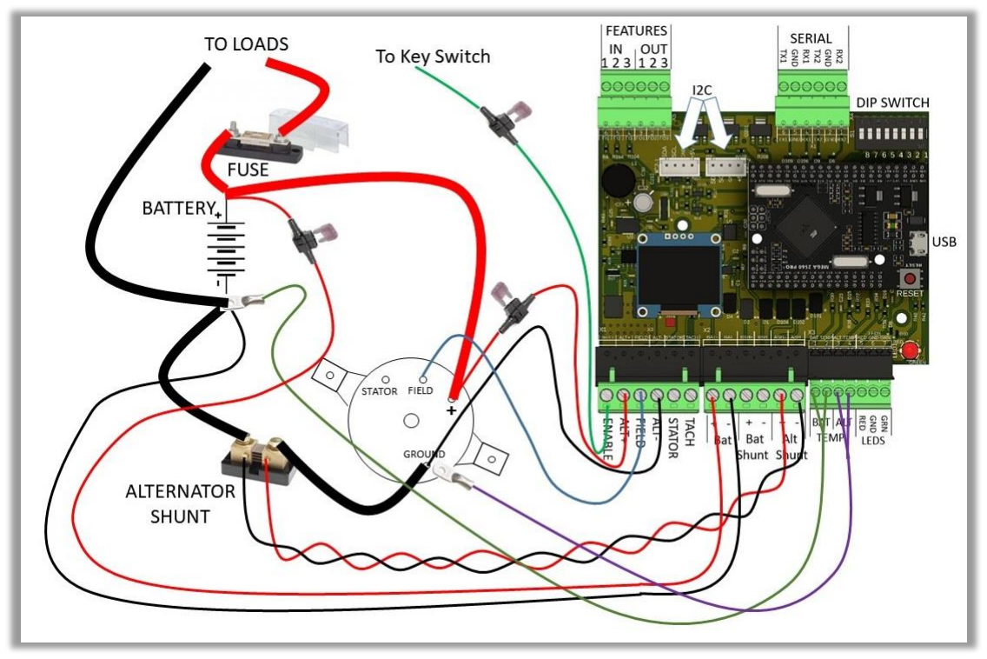
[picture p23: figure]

Figure 8: Alternator-centric, Single-shunt Installation

## CONFIGURING THE VSR MINI MEGA ALTERNATOR REGULATOR

The simplest way to configure your VSMMAR is via the DIP switches. With these you can select one of the default Charge Profile Entries (CPE), as well as tell the regulator the size of the battery bank you have (needed to more accurately decide when the battery is full).

### USING THE DIP SWITCHES

Many of the basic features of the VSMMAR can be configured using the DIP switches. Advanced changes may be made via edits to the source code files or by using the ASCII serial commands (See: Error! Reference source not found. ). The following table defines how the DIP switches are used:

Position | Meaning (Regulator Version 3)
1..3 <1> <2> <3> Off, Off, Off On, Off, Off Off, On, Off On, On, Off Off, Off, On On, Off, On Off, On, On On, On, On | Select Charge profile 1..8 1 = Default (Safe) Lifeline AGM (also known as Concord AGM) 2 = Flooded Lead Acid #1 (Starter type , etc.) 3 = Flooded Lead Acid #2 (HD - Storage type) 4 = AGM #2 (Higher charge voltages) 5 = GEL 6 = Carbon Foam (Firefly) 7 = Custom (Changeable – Preconfigured HD Storage with Overcharge) 8 = LiFeP04) (See Table 6 for more details)
4,5 <4> <5> Off, Off On, Off Off, On On, On | Define Battery Capacity as: ** 1x, – 250Ah 2x, 250Ah – 500Ah 3x, 500Ah – 750Ah 4x. 750Ah and above
6 | On – Use Small Alternator Mode Off – Use Large Alternator Mode Small Alternator Mode will restrict the maximum alternator output to 75% of its amperage capability. Large Alt mode limits output to 100%.
7 | On - Enable Tach Mode Off – Disable Tach Mode
8 | Factory Reset (with FEATURE_IN_RESTORE asserted at startup)

Figure 9: DIP Switch Settings

### USING ASCII COMMANDS

In addition to the DIP switches, many parameters of the VSMMAR can be customized by sending in a series of ASCII commands via a USB cable attached to the Mini Mega 2650 processor daughter card.

Changes sent to the VSMMAR are saved in flash memory on the CPU for use next time the regulator starts up. (See Sequence of Operation section below for more details). Because of this you will need to restart the regulator after you have finished sending it ASCII change commands before those changes will take effect. There are some exceptions, such as the $FRM Force Regulator Mode command, $EBA – External Battery Amps, and a few more. See details of each command below.

COMMUNICATING WITH THE ARDUINO SHIELD ALTERNATOR REGULATOR

The VSMMAR supports external communication of status and more advanced configuration changes than the DIP switches allow. Communications is primarily via serial ASCII strings, the formats of which are documented in the “VSMMAR Systems – Communications and Programming Guide, via the USB connector on the Mini Mega processor daughter board.

At this time, the VSMMAR is not compatible with the WS500 Configuration Tool available from Off Grid Software Solutions who also sell a commercial version of the VSR Alternator Regulator: https://offgridsoftwaresolutions.com/product-category/software/

### TUNING USING SOURCE CODE

As a final configuration method, the source code may be directly modified, recompiled and then flashed into the VSMMAR. This gives the ultimate flexibility, as well as the ultimate responsibility.

It is best to conduct this editing with Microsoft Visual Studio Code and PlatformIO. The Github files include the appropriate development environment configurations include the variant files needed to support the Mini Mega Pro daughter card and the Platformio.ini files necessary for configuring the environment and libraries.

The first place to start for basic configuration and turning is the Config.h file. Next, study the System.cpp file. Take care to completely understand the code and the implications of each setting before making any changes. To put things into perspective, I spent several years working with this code in order to create the refactored code while not breaking any of Al’s great work on the underlying operation of the regulator. Step slowly and carefully.

Figure 10: Default Charge Profiles

### FEATURE-IN AND FEATURE-OUT PORTS

### FEATURE-IN PORTS

Feature-in ports are enabled by connecting the feature-in pins to a voltage greater than 6v. Voltages as high as 72v are allowed. Feature-in ports can serve several purposes. The function of each feature-in port can be altered using various #define compile options in the source.

OPTIONS FOR FEATURE-IN PORTS
In the source code there are several optional uses of the feature-in ports. These are enabled in the source file Config.h via first selecting different #define statements (uncommenting them) to active the feature, then editing, as desired, the immediately following FEATURE_IN_PORT(number) entry, and finally recompiling the source, and re-flashing the firmware. The following options are included in the source; each is explained in more detail below:
- | #define FEATURE_IN_RESTORE | - Restore settings to “factory defaults” *see special
| instructions below
- | #define FEATURE_IN_EQUALIZE | - Initiate equalization charge
- | #define FEATURE_IN_SCUBA | - Enable reduction of PWM field drive
- #define FEATURE_IN_FORCE_TO_FLOAT - Keeps regulator in float charge mode

FEATURE_IN_RESTORE
This feature is only checked at start-up of the VSMMAR, that is, when ENABLE is powered or after the reset button on the processor board is pressed (or the system conducts a reset due to a fault condition). To force such a restore, three conditions must be true at this time:
1- DIP switch 8 must be in the ON position
2- The assigned Feature-in port must be held high (at battery voltage)
3- The systemConfig.CONFIG_LOCKOUT in System.cpp must not be set to 2.

After conducting such a restore, reset DIP switch 8 to the OFF position and remove the power from the assigned Feature-in port.

Note: The Feature-in port assigned to the restore feature can also be assigned to another Feature-in function. This is because this port is checked both at start-up and in the main loop of the program. Of course, if one is intending to use this port for another function, and not intending to initiate a restore at boot time, DIP switch 8 should be set to OFF.

FEATURE_IN_EQUALIZE
If CPE #1 through 7 is selected, when this Feature-in port is held high and the alternator running, equalize mode will be enabled provided the charge profile (CPE) includes an equalization voltage setting. Once this feature is activated, the equalization will continue until any of the following is true:
1- the assigned Feature-in port is no longer held high;
2- defined exit Amps have been met; or
3- defined timeout has been met.

Note: Equalize is considered a high-monitoring mode and there is a potential for damage to the batteries. As such, the Feature-in port must be in an inactive state (low) and then transition to high in order for equalize to be recognized. This is to prevent the possibility of someone accidentally leaving the equalize Feature-in switch turned on. Once equalize mode has been entered, the Feature-in port must remain connected to VBat and the status LED(s) will blink-out the equalize status pattern. This Feature-in function is ignored if the charge profile (CPE) is #8.

FEATURE_IN_SCUBA
This feature exists to force the field PWM output to a lower level while not changing the charge mode. It is useful for small engines when a SCUBA compressor, water maker, or other substantial load can be switched on, loading down the engine. When this Feature-in port is held high, the PWM field drive will be set to a pre-set lower level, defined by FIELD_PWM_SCUBA in Config.h. The range of this value is 0 to 255. To calculate this number, starting with the percentage of maximum PWM, the calculation would be: (Percentage * 255)/100 … rounded to an integer.

FEATURE_IN_FORCE_TO_FLOAT
This feature exists to allow an external input (a switch or a signal) to override the charge mode and activate float mode until the assigned Feature-in port is returned to a low state. This is useful for reducing engine load or to protect LiFePO4 batteries (if the LiFePO4 battery management system (BMS) has a digital shutdown (or alarm state) output. (Also see FEATURE_OUT_LIFEPO_SHUTDOWN_ALARM below).

### FEATURE-OUT PORTS

Each of the three Feature-out ports of the VSMMAR provide an open-collector driver and can used for any of several functions. Open-collector means that when the Feature-out port is active, the port provides a ground and when the Feature-out port is inactive, the port is a high-impedance point, neither high nor low. Feature-out ports are active Low and are limited to 0.5 amp on each of the feature-out connectors, but ideally would be limited to that maximum total amongst the three Feature-out ports. This is not only due to the thermal limits of the output transistors, but also because the return line (battery -) is shared by the Feature-out and the VBat voltage sensing. Placing too much return current via the feature-out connectors can impact the accuracy of measured battery voltages.

OPTIONS FOR FEATURE-OUT PORTS
In the source code there are several optional uses of the Feature-out ports. These are enabled in the source file Config.h via first selecting different #define statements (uncommenting them) to active the feature, then editing, as desired, the immediately following FEATURE_IN_PORT(number) entry, and finally recompiling the source, and re-flashing the firmware. The following options are included in the source; each is explained in more detail below:
- | #define FEATURE_OUT_LAMP | - Enable LAMP / Fault driver
- | #define FEATURE_OUT_RED_LED | - Echo the on-board red LED to the designated feature-out
| | port

- | #define FEATURE_OUT_GREEN_LED | - Echo the on-board green LED to the designated feature- out port
- | #define FEATURE_OUT_ENGINE_STOP | - Active when we enter FLOAT mode.
- #define FEATURE_OUT_LIFEPO_SHUTDOWN_ALARM - An output for an alarm buzzer, light, etc.
- | #define FEATURE_OUT_COMBINER | - Allows sharing of charging source(s) between two batteries.

Example of code:

#define FEATURE_OUT_RED_LED | // Enable feature to echo the green LED to the feature out por

t

#ifdef FEATURE_OUT_RED_LED

#define RED_LED_FO_PORT FEATURE_OUT_PORT2 | // Set the feature_out_port to use for the Green LED output fe

ature

#endif

//#define FEATURE_OUT_ALT_LAMP | // Enable FEATURE_OUT port as an ALTERNATOR LAMP driver, to sh

ow rough

| // alternator status as well as blink out the FAULT code

#ifdef FEATURE_OUT_ALT_LAMP

#define ALT_LAMP_FO_PORT FEATURE_OUT_PORT3 // This sets the feature_out_port of the Alternator Lamp featu

re

#endif

REGARDING LEDS AND “LAMP”
The on-board LED(s), LEDs ports, FEATURE_OUT_LAMP, FEATURE_OUT_RED_LED, and FATURE_OUT_GREEN_LED, these may at first glance seem to be duplicate features. In fact though, there are some important and useful differences between these options.

On-board Led: The on-board LED can either be a bi-color 5mm LED or one each red and green SMD LEDs. Red flashing patterns of this LED indicate fault codes. Green flashing patterns of this LED indicate charge modes.

LED ports: The three-pin LED port (Red, Gnd, Grn) can be used to directly drive an LEDs which duplicate the on-board LED(s). A series resistor is not necessary, unless a dimmer LED is desired.

FEATURE_OUT_LAMP
With this feature enabled, a Feature-out port can be set to drive a dash mounted ‘Alt’ lamp. The port will be disabled (lamp off, port high), unless in one of the following conditions:
- Indication of no-charging status – lamp will be full on during this time. (e.g., during engine warm-up period)
- Fault status – lamp will blink-out fault codes if OUT_LAMP_MIRROR_FAULT is defined to true
- Controller resetting – lamp will blink-out resetting LED pattern if OUT_LAMP_MIRROR_RESETTING is defined to true

- Regulator is in EQUALIZE mode – Lamp will blink-out Equalize LED pattern, if OUT_LAMP_MIRROR_EQUALIZE is defined to true

So for those of us who are old enough to remember the single red alternator light on the dash of their VW or other car… if all of the OUT_LAMP_MIRROR options are set to false, the lamp output will somewhat mimic those old alternator lamps and be on when the alternator is not outputting current. (It will not dim. It will only be either on or off).

With all or some of the OUT_LAMP_MIRROR options set to true (in Config.h), the FEATURE_OUT_LAMP will provide a combination of the old “alt lamp” and a digital report of key status or fault conditions.

FEATURE_OUT_RED_LED, FEATURE_OUT_GREEN_LED
With either of these options enabled, the designated Feature-out ports will follow the respective on-board status LED(s). This option is provided in addition to the LED ports so lights other than LEDs can be used (for example incandescent lamps already existing in an engine gauge panel).

FEATURE_OUT_LIFEPO_SHUTDOWN_ALARM
With this this option enabled, a designated Feature-out port will become active if the FEATURE_IN_FORCE_TO_FLOAT port is defined and active. This could be useful to provide a separate alarm (buzzer or light) if the FEATURE_IN_FORCE_TO_FLOAT port was being driven by a digital alert from a BMS.

FEATURE_OUT_ENGINE_STOP
With this option enabled, a designated Feature-out port will become active for a designated number of milliseconds, the ENGINE_STOP_PULSE_DURATION, once the alternator enters float, forced-float, or post-float mode. This can be used to stop a generator or to provide a “done” alert.

FEATURE_OUT_ENGINE_COMBINER
With this option enabled, the VSMMAR can provide a battery combiner function via a designated Feature-out port. The following is a detailed explanation of the rationale and settings for using this option.

Many situations have more than one battery bank, such as a starter battery and a “house” bank, but only one alternator. Or there might have two batteries, each with its own alternator. An example might be a boat that has a large battery bank for the house battery, and a smaller battery used for the starter, or a bow thruster, or for a windlass. Using the one of the Feature-out ports to drive a high-current, continuous-duty relay or contactor is an inexpensive way to get a ‘smart’ battery combiner. There are perhaps two common reasons for using a battery combiner:
1. Allow a second charging source to ‘help’ recharge the large house battery during its bulk phase
2. Recharging a second battery which has no charging source of its own.

Because the VSMMAR is designed to focus on the attached battery, and not the ‘combined in’ battery, some assumptions must be made and care taken. We want to make sure we do not overload a second alternator, or overcharge a second battery. Some additional considerations which must be taken into account:

- Do not exceed the current limit of the Feature-out port (0.5 amp) with the coil draw of the external large relay. (Using an intermediate low-current relay to drive the coil or a higher coil current combiner relay might be necessary).
- Use a length of medium size wire (e.g., 10’ of 10g wire) to ensure a low level of resistance between the two batteries. A minimum resistance of 5-10mΩ (milli-ohm) appears to be common.

Situation #1: Recharging a second battery which has no charging source of its own (most common situation)
In this example, there are still two independent batteries, but only one charging source. A representative example would be a house battery / alternator being controlled by VSMMAR, and a second battery used for engine starting or to power a bow-thruster. Unlike the case below where we are looking to gain assistance from the other battery/alternator, in this case the one alternator is being asked to be the charging source for the second battery.

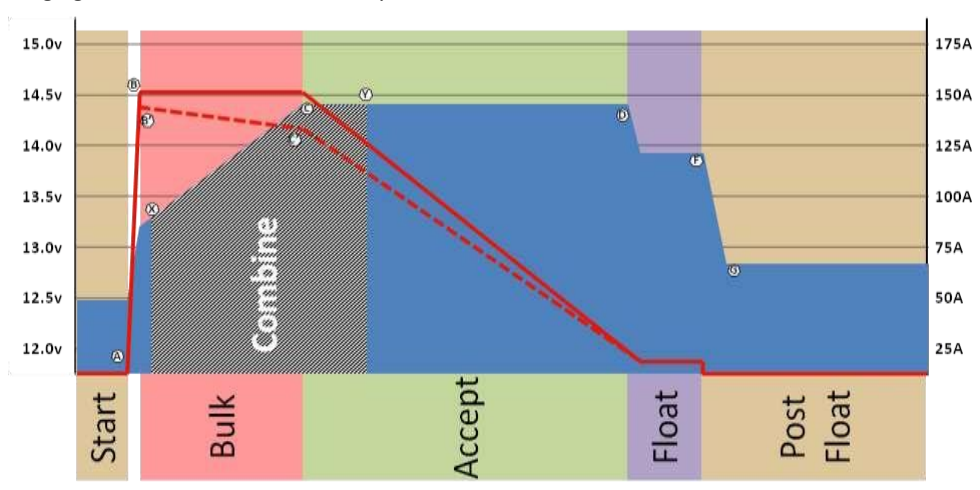
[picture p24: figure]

Figure 10: Charging second battery combiner profile

Figure 11 illustrates the conditions when we want the combiner enabled. The idea is the second battery parallels the charge profile of the main battery, and because we are not actively managing the second battery we cut off the acceptance phase after a relatively short time (Points ‘C’ to ‘Y’ above) to reduce the risk of overcharging the second battery, in effect boiling it off.

Care must be taken in each of these situations to protect the second battery and/or second charging system. Remember the VSMMAR will focus on its battery and adjust things to that battery’s needs with no regard to the other battery’s needs, outside of the limited combiner configuration options.

Situation #2: Using second battery/alternator to ‘help’ the house battery during bulk charging phase.
In this example, there are two fully independent batteries and associated charging systems, perhaps the factory alternator and starter battery, and a house battery with its own alternator using the VSMMAR. The starter battery will likely be quickly recharged after the engine starts, leaving a significant amount of unused capacity in the starter battery’s alternator (or visa versa).

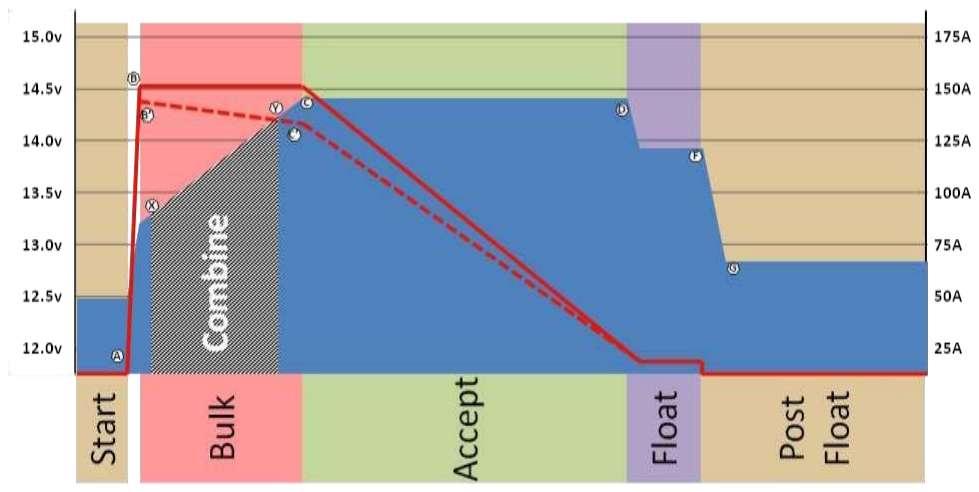
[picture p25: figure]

Figure 11: Receiving Help combiner profile

In this mode, Figure 12 above illustrates when we want to combine the two systems (between points ‘X’ and ‘Y’).
Specifically during Bulk, we want to:
- Wait until the house battery reaches 13.2v before enabling the combiner. If we combined sooner there is a risk of pulling energy from the second battery, as opposed to only asking the second alternator to share its capacity. 13.2v will also reduce the voltage difference between the two batteries thereby minimizing initial surge current.
- Break the connection of the two batteries after 14.2v. With the assumption the second battery has its own charging source that will handle all the recharging needs of that battery, we do not want to ‘override’ those decisions. 14.2v was selected under the assumption that many ‘starter’ batteries are connected to a default internally regulator fixed voltage alternator; those are often in the 13.8 to 14.2v range.

COMBINER CONFIGURATION OPTIONS
All options for configuring the Feature-out port as a combiner are made in the source code file Config.h, there are no ASCII commands to modify these. In Config.sys, there are two combiner profiles: COMBINER_PROFILE_LIFEPO and COMBINER_PROFILE_OTHER. Only one should be defined and the other #define statement commented out.

The following variables in the source code for COMBINER_PROFILE_OTHER:
#define | COMBINE_CUTIN_VOLTS | 13.2

#define | COMBINE_HOLD_VOLTS | 13.0

#define | COMBINE_CUTOUT_VOLTS | 14.2

#define | COMBINE_ACCEPT_CARRYOVER 0.75*3600000UL // ¾ an hour, 45 minutes.

Once voltage raises to the COMBINE_CUTIN_VOLTS level (13.2 by default) – point ‘X’ in the figures above - the combiner will be enabled (via a Feature-out port), and will stay enabled even if the battery voltage temporarily dips – as long as it remains at or above the COMBINE_HOLD_VOLTS level (13.0v by default). However, if it drops too much and goes below the HOLD level, the combiner will be disabled.

As battery voltage rises, the combiner will be disabled by either the voltage rising above the COMBINE_DROPOUT_VOLTS level – point ‘C’ shown in the figures above (14.2v by default), or after being in the acceptance phase for the COMBINE_ACCEPT_CARRYOVER duration – point ‘Y’ shown in t. Either point (along with low voltage) will cause the combiner to open.

Note that as with all charge profile entries (CPEs), voltages shown above are ‘normalized’ to a 12v battery and will automatically scale by the system voltage multiplier. (e.g., in a 24v system, the multiplier is 2, so the combine voltage becomes 2 * 13.2v, or 26.4v).

## OPERATION OVERVIEW

The Arduino Shield Alternator Regulator has a wide range of flexibility and can be configured in three ways, ranging from simple to anything-goes.

- Select among built-in (default) parameters via the DIP switches
- Modify many of the built-in parameters via sending ASCII commands over the USB port
- Modifying any or all built-in parameters in the source code, recompiling, and re-flashing to the processor board.
(requires use of USB port and Arduino (www.arduino.cc) or other compatible IDE such as PlatformIO on Visual Studio Code, the IDE used for the refactoring of the VSMMAR code)

### START-UP SEQUENCE

When the VSMMAR is first powered up it loads the default setting from the firmware and then looks to the DIP switches to see what the user has selected. It will then samples the system voltage to decide if it is installed in a 12v or 24v environment (and thereby setting the SysVolt multiplier, see SST: / System Status below for more details about this and how it is used). If the VSMMAR is installed in higher voltage battery system that a nominally 24V system, the boot process will abort and the processor will be rebooted. Finally, it will look at the saved flash memory in the CPU to see if any of the parameters have been modified or any of the DIP switches have been overridden by the user using ASCII commands.

Note that parameters saved to flash are only checked during startup; this is why after changing any parameters via an ASCII string command you need to reset the regulator (via the $RBT – ReBooT command) in order for any of those parameters to take effect. This is done this way so that the regulator does not start acting on changes part way through you making configuration changes. For example, if you are updating the CPE entry, you want to update and verify all parts of it before the regulator starts using the new values.

### RAMP-UP SEQUENCE

Next, the regulator will enter the ramp-up phase. It first waits 15 seconds before doing anything (configurable: systemConfig.ENGINE_WARMUP_DURATON in System.cpp) to give the engine time to start. Finally it will begin to slowly ramp up the alternator field over a period of about a minute(configuarable:
PWM_RAMP_RATE in SmartRegulator.h) before entering bulk phase.

### CHARGING THE BATTERY

Once the regulator has completed its startup and ramping sequence it enters the ‘charging’ phases. Each phase has limits (e.g., voltage, amps, etc.) as well as ‘exit’ criteria based on voltage, amps and/or time. A high degree of configurability allows each phase to be used, or bypassed as needed to meet the battery manufacturer’s recommended charging profile. While in each of these phases the regulator will also monitor battery and alternator temperature, making adjustments as required. It will also look to see if the regulator has been configured with system limits and make sure none of those are exceeded.

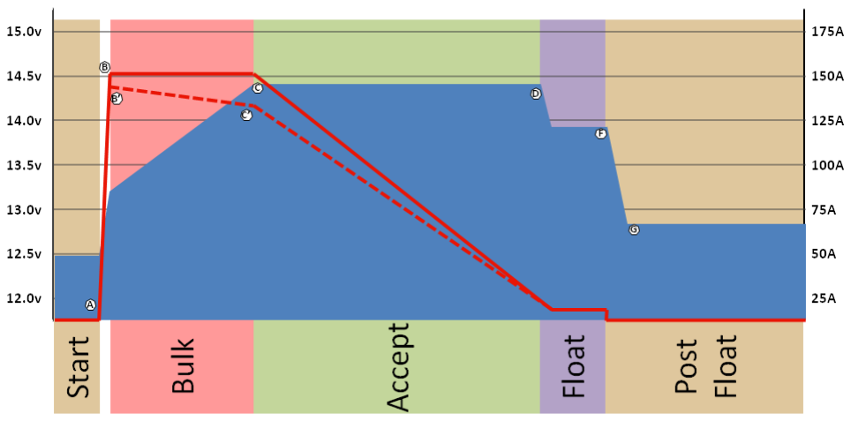
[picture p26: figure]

Figure 12: Example 3-stage Charge profile

Figure 13, above, shows a typical 3-phase charge profile, consisting of the Bulk, Acceptance, and Float state. The red lines correspond to amps and the right axis. The shaded bars correspond to volts and the left axis. This is one of the simplest charge profiles, and very commonly seen in external regulators. The following table details each phase as well as the parameters in the source which can impact them.

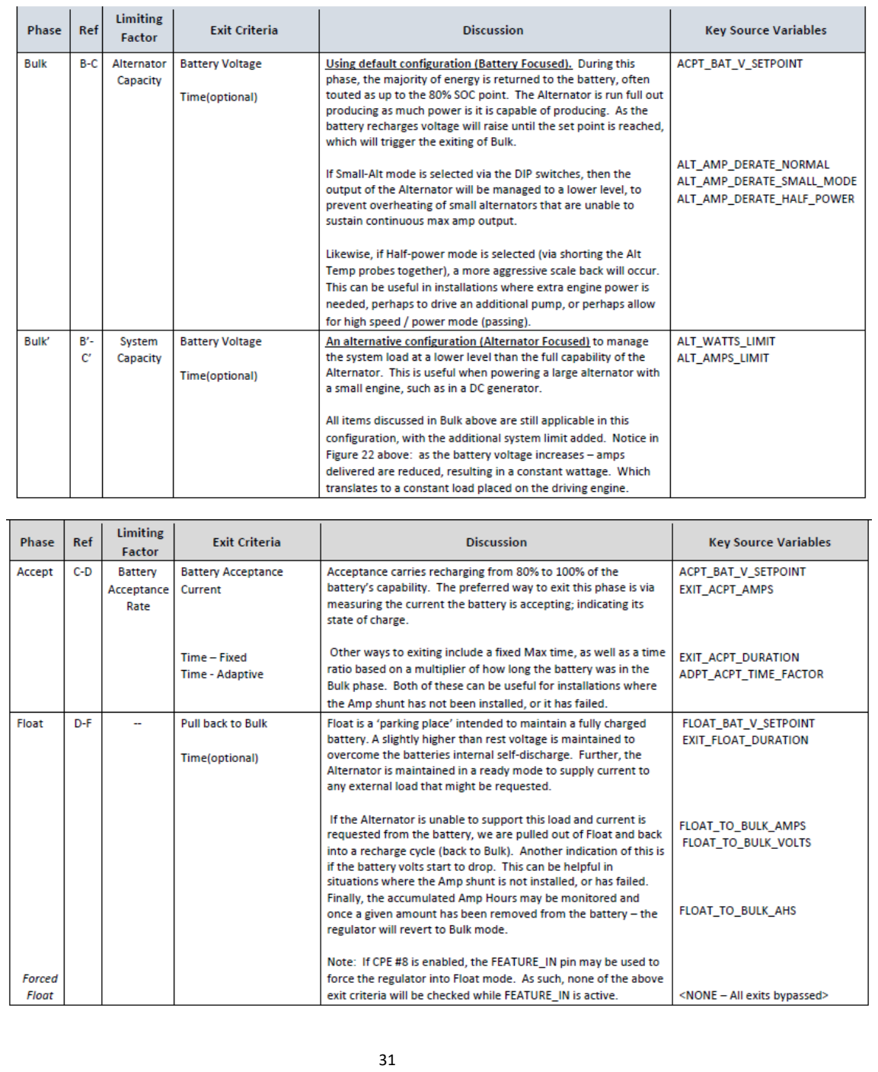
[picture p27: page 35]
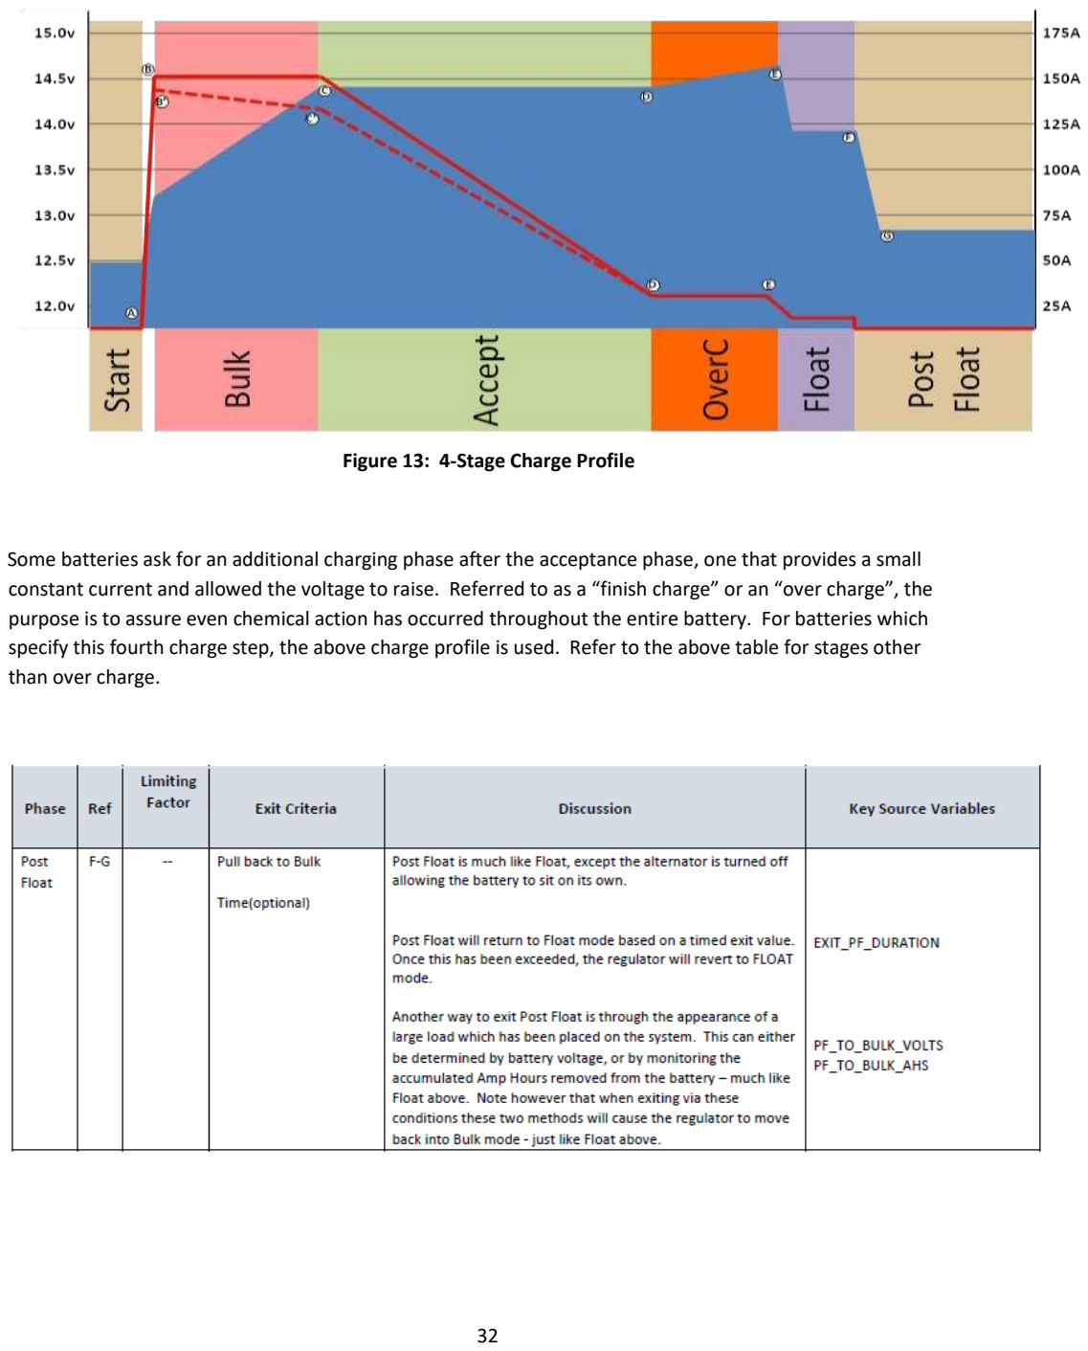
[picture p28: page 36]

Figure 13: 4-Stage Charge Profile

Some batteries ask for an additional charging phase after the acceptance phase, one that provides a small constant current and allowed the voltage to raise. Referred to as a “finish charge” or an “over charge”, the purpose is to assure even chemical action has occurred throughout the entire battery. For batteries which specify this fourth charge step, the above charge profile is used. Refer to the above table for stages other than over charge.

Note how the VSMMAR will move directly to acceptance phase if the battery voltage quickly rises. This, combined with the measurement of the acceptance current to determine if a battery is fully charged, handles the all too common situation of being plugged into shore power and subsequently getting under way with the battery already fully charged. Traditional time-only based regulators might be stuck in the acceptance phase for several hours until the fixed-time limit is reached, overcharging the battery. With the VSMMAR, the regulator will recognize quickly that the battery is fully charged and move into float mode within seconds of the engine starting. This eliminates one of the major ways a less intelligent regulator can damage your batteries.

Each of the charge steps are fully configurable, and many can be bypassed (e.g., most charge profiles do not use

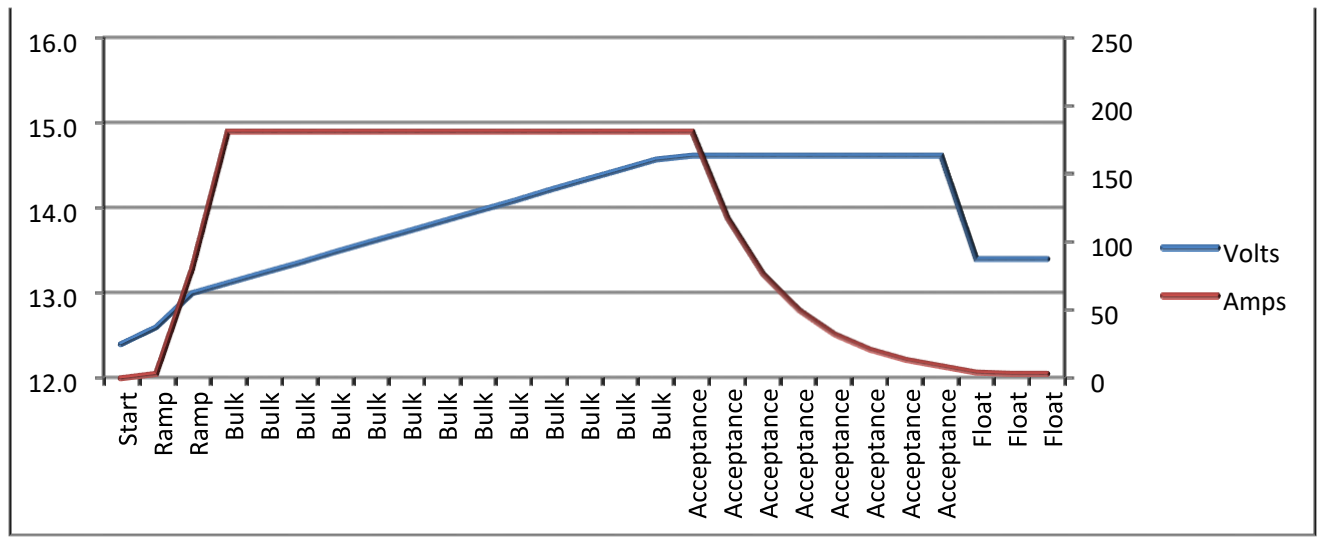
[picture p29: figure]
Volts; Amps

the overcharge step). As way of an example, the following two diagrams show two different approaches for charging a heavy duty 12v / 500Ah battery (e.g., two L-16 batteries). Both profiles are included in the default VSMMAR CPEs as profiles #3 and #6. Figure 14 shows the traditional 3-step charge profile (bulk, accept, and float), while Figure 15 illustrates the flexibility to accommodate a 4-step charge profile (bulk, accept, over-charge, and float). The diagrams provide an overview of each phase and represent an 180A alternator charging a 12v 500Ah battery.
Figure 14 – Example – 3-Stage Profile - Charge profile #3 (HD FLA )

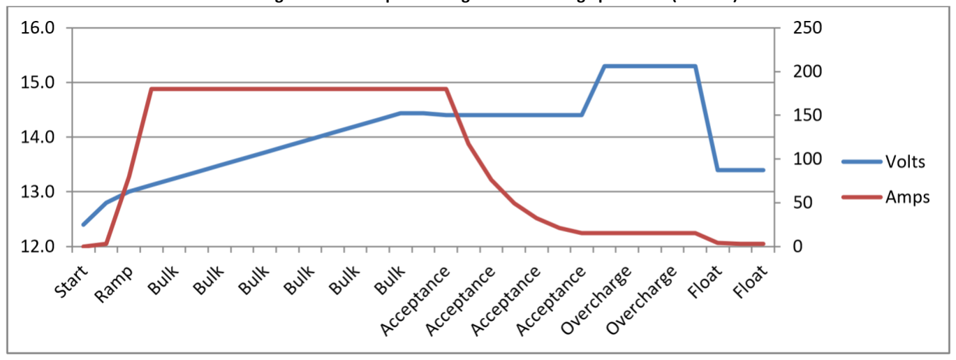
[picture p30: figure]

Figure 15 – Example – 4-Stage Profile -CPE #6 (HD FLA - Alternative Charge Profile)

## CHARGING LiFePO4 BATTERIES

To be written

## RESTORE TO AS-COMPILED (DEFAULT) STATUS

Configurations (system and Charge parameters) which have been changed from the as-compiled default values may be restore in one of three ways:

- Individually by the $CPR:n , $SCR: and $CCR: commands.
- Collectively via the $MSR: command.
- Total system restore is accomplished by:
1: Connecting a Feature-in port which has be configured for the FEATURE_IN_RESTORE function in Config.h to Vbat (battery positive voltage) before applying power to the regulator, AND
2: setting DIP switch 8 to ON, AND
3: then applying power.
This will restore all configurations to the default condition.

If the regulator has been locked out via the $SCO command the only way to restore to the default configuration is via using the Feature-in restore procedure, because none of the ASCII change commands will function once the regulator has been locked. You may also clear the locked flag by recompiling the firmware and reloading it. If you do this, you will need to make a change to the following defines in the Flash.h file of the source code to some other random value:
#define | SCS_ID1_K 0xFC3A

#define | SCS_ID2_K 0x69D3

These provide a validation token at the beginning of each saved block of data in the flash memory. If you do not change these values the CPU will read the existing FLASH and finding a match to the above keys will assume the saved parameters are valid. (Including the locked-out bit). So, in order to ‘clear’ the flash memory, you must change the tokens. … So avoid the hassle and don’t lock out changes with the $SCO command.
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

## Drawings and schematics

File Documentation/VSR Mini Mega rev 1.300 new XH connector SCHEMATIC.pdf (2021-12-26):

# 10 GND BAT54S

VDD GND | GND | GND

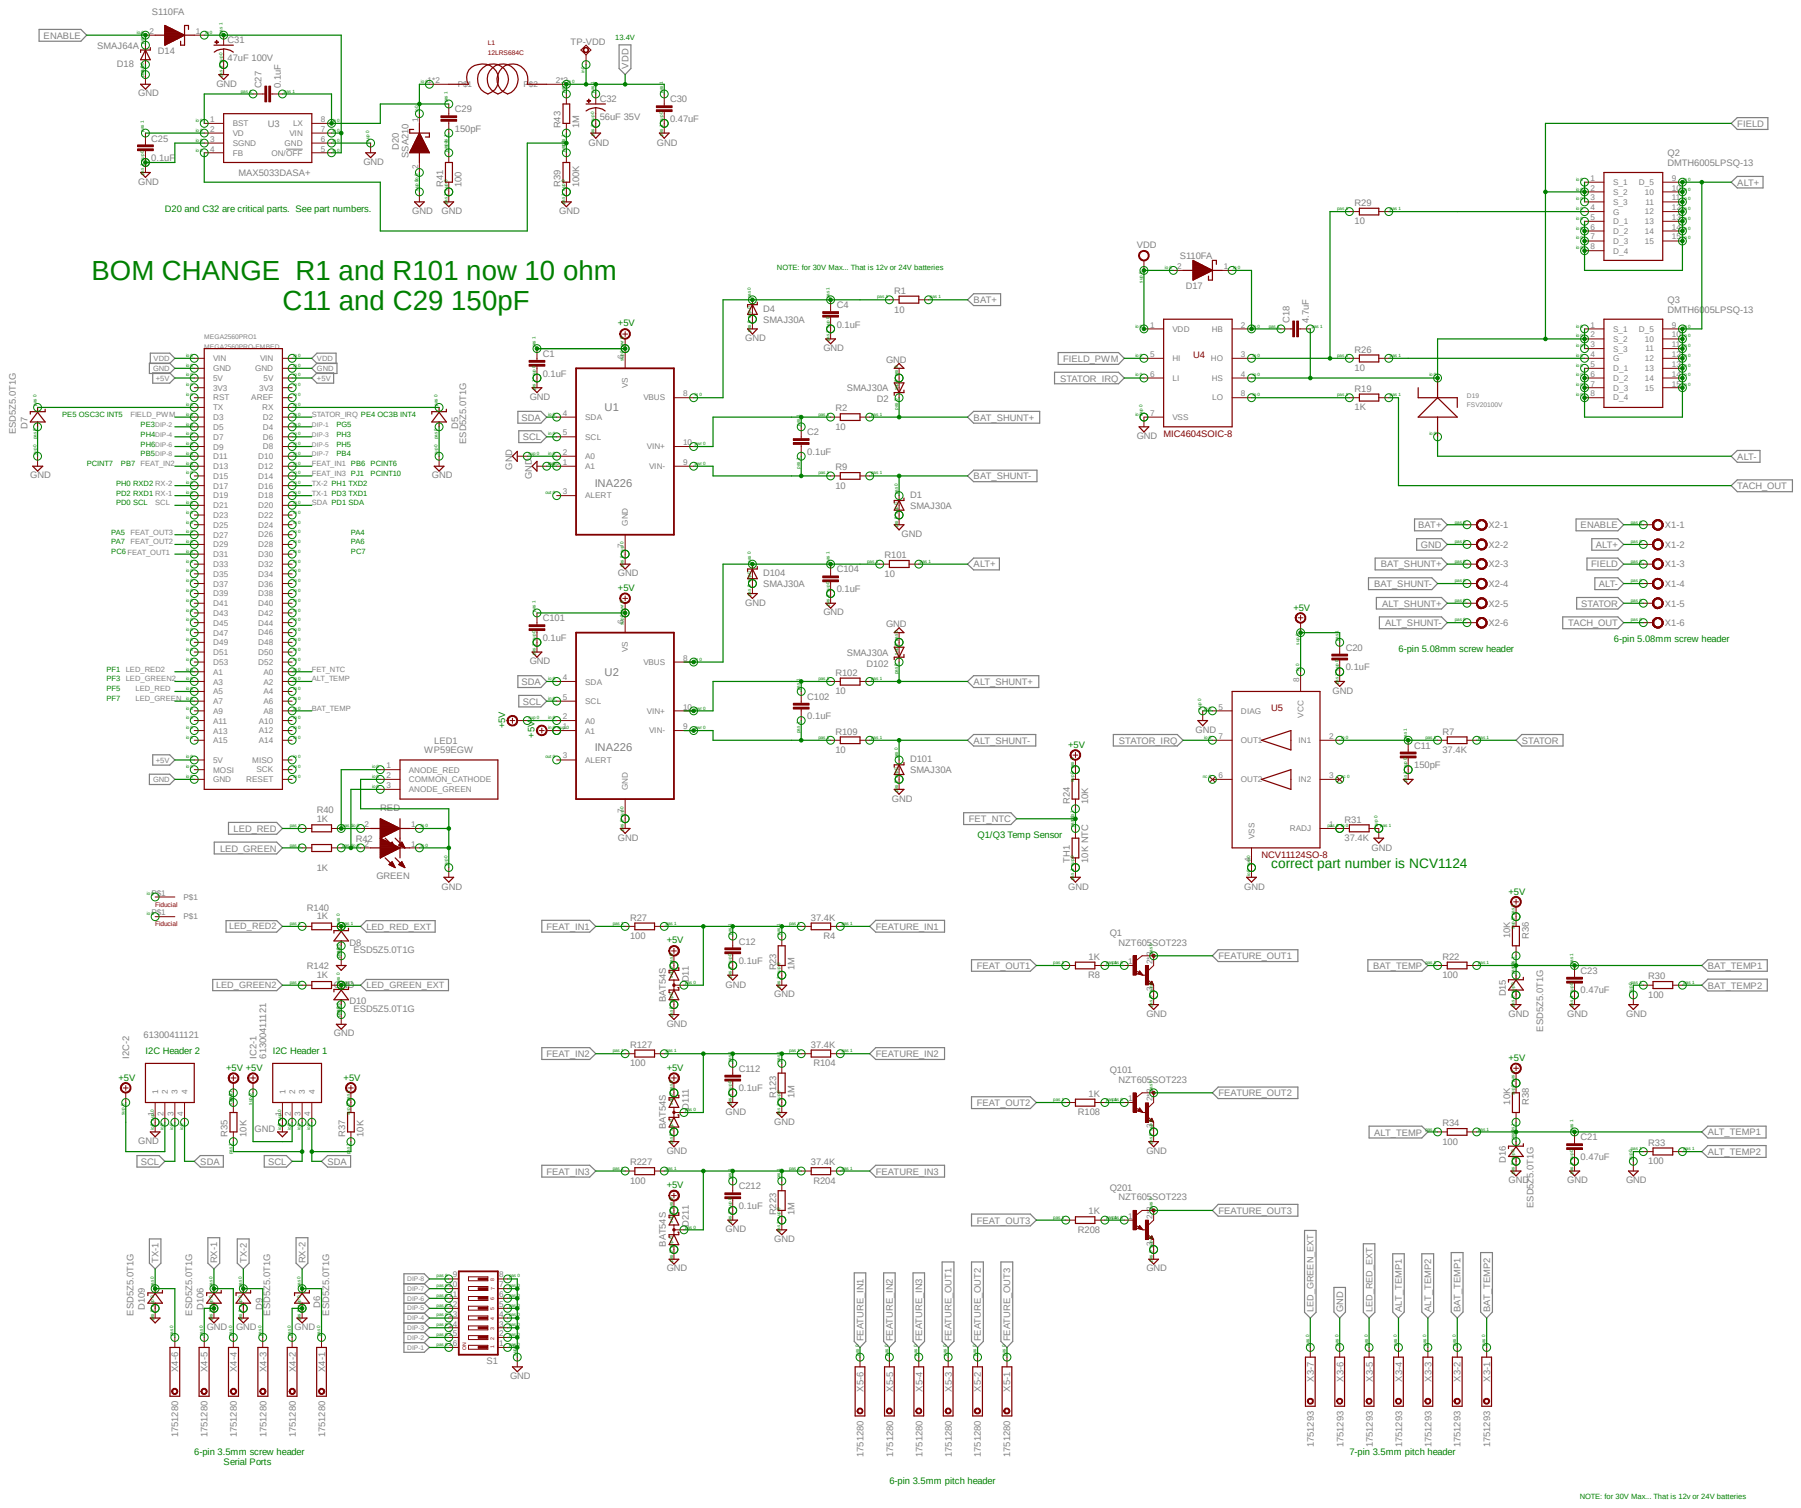
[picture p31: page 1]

BOM CHANGE R1 and R101 now 10 ohm

6 VIN+ 10 VIN- 9 SCL 5 VBUS 8 A0 2 A1 1 ALERT 3 GND

6-pin 5.08mm screw header

correct part number is NCV1124 PF5 PF7

37.4K GND ¹⁰K 10K NTC GND

6-pin 3.5mm screw header Serial Ports

NOTE: for 30V Max... That is 12v or 24V batteries

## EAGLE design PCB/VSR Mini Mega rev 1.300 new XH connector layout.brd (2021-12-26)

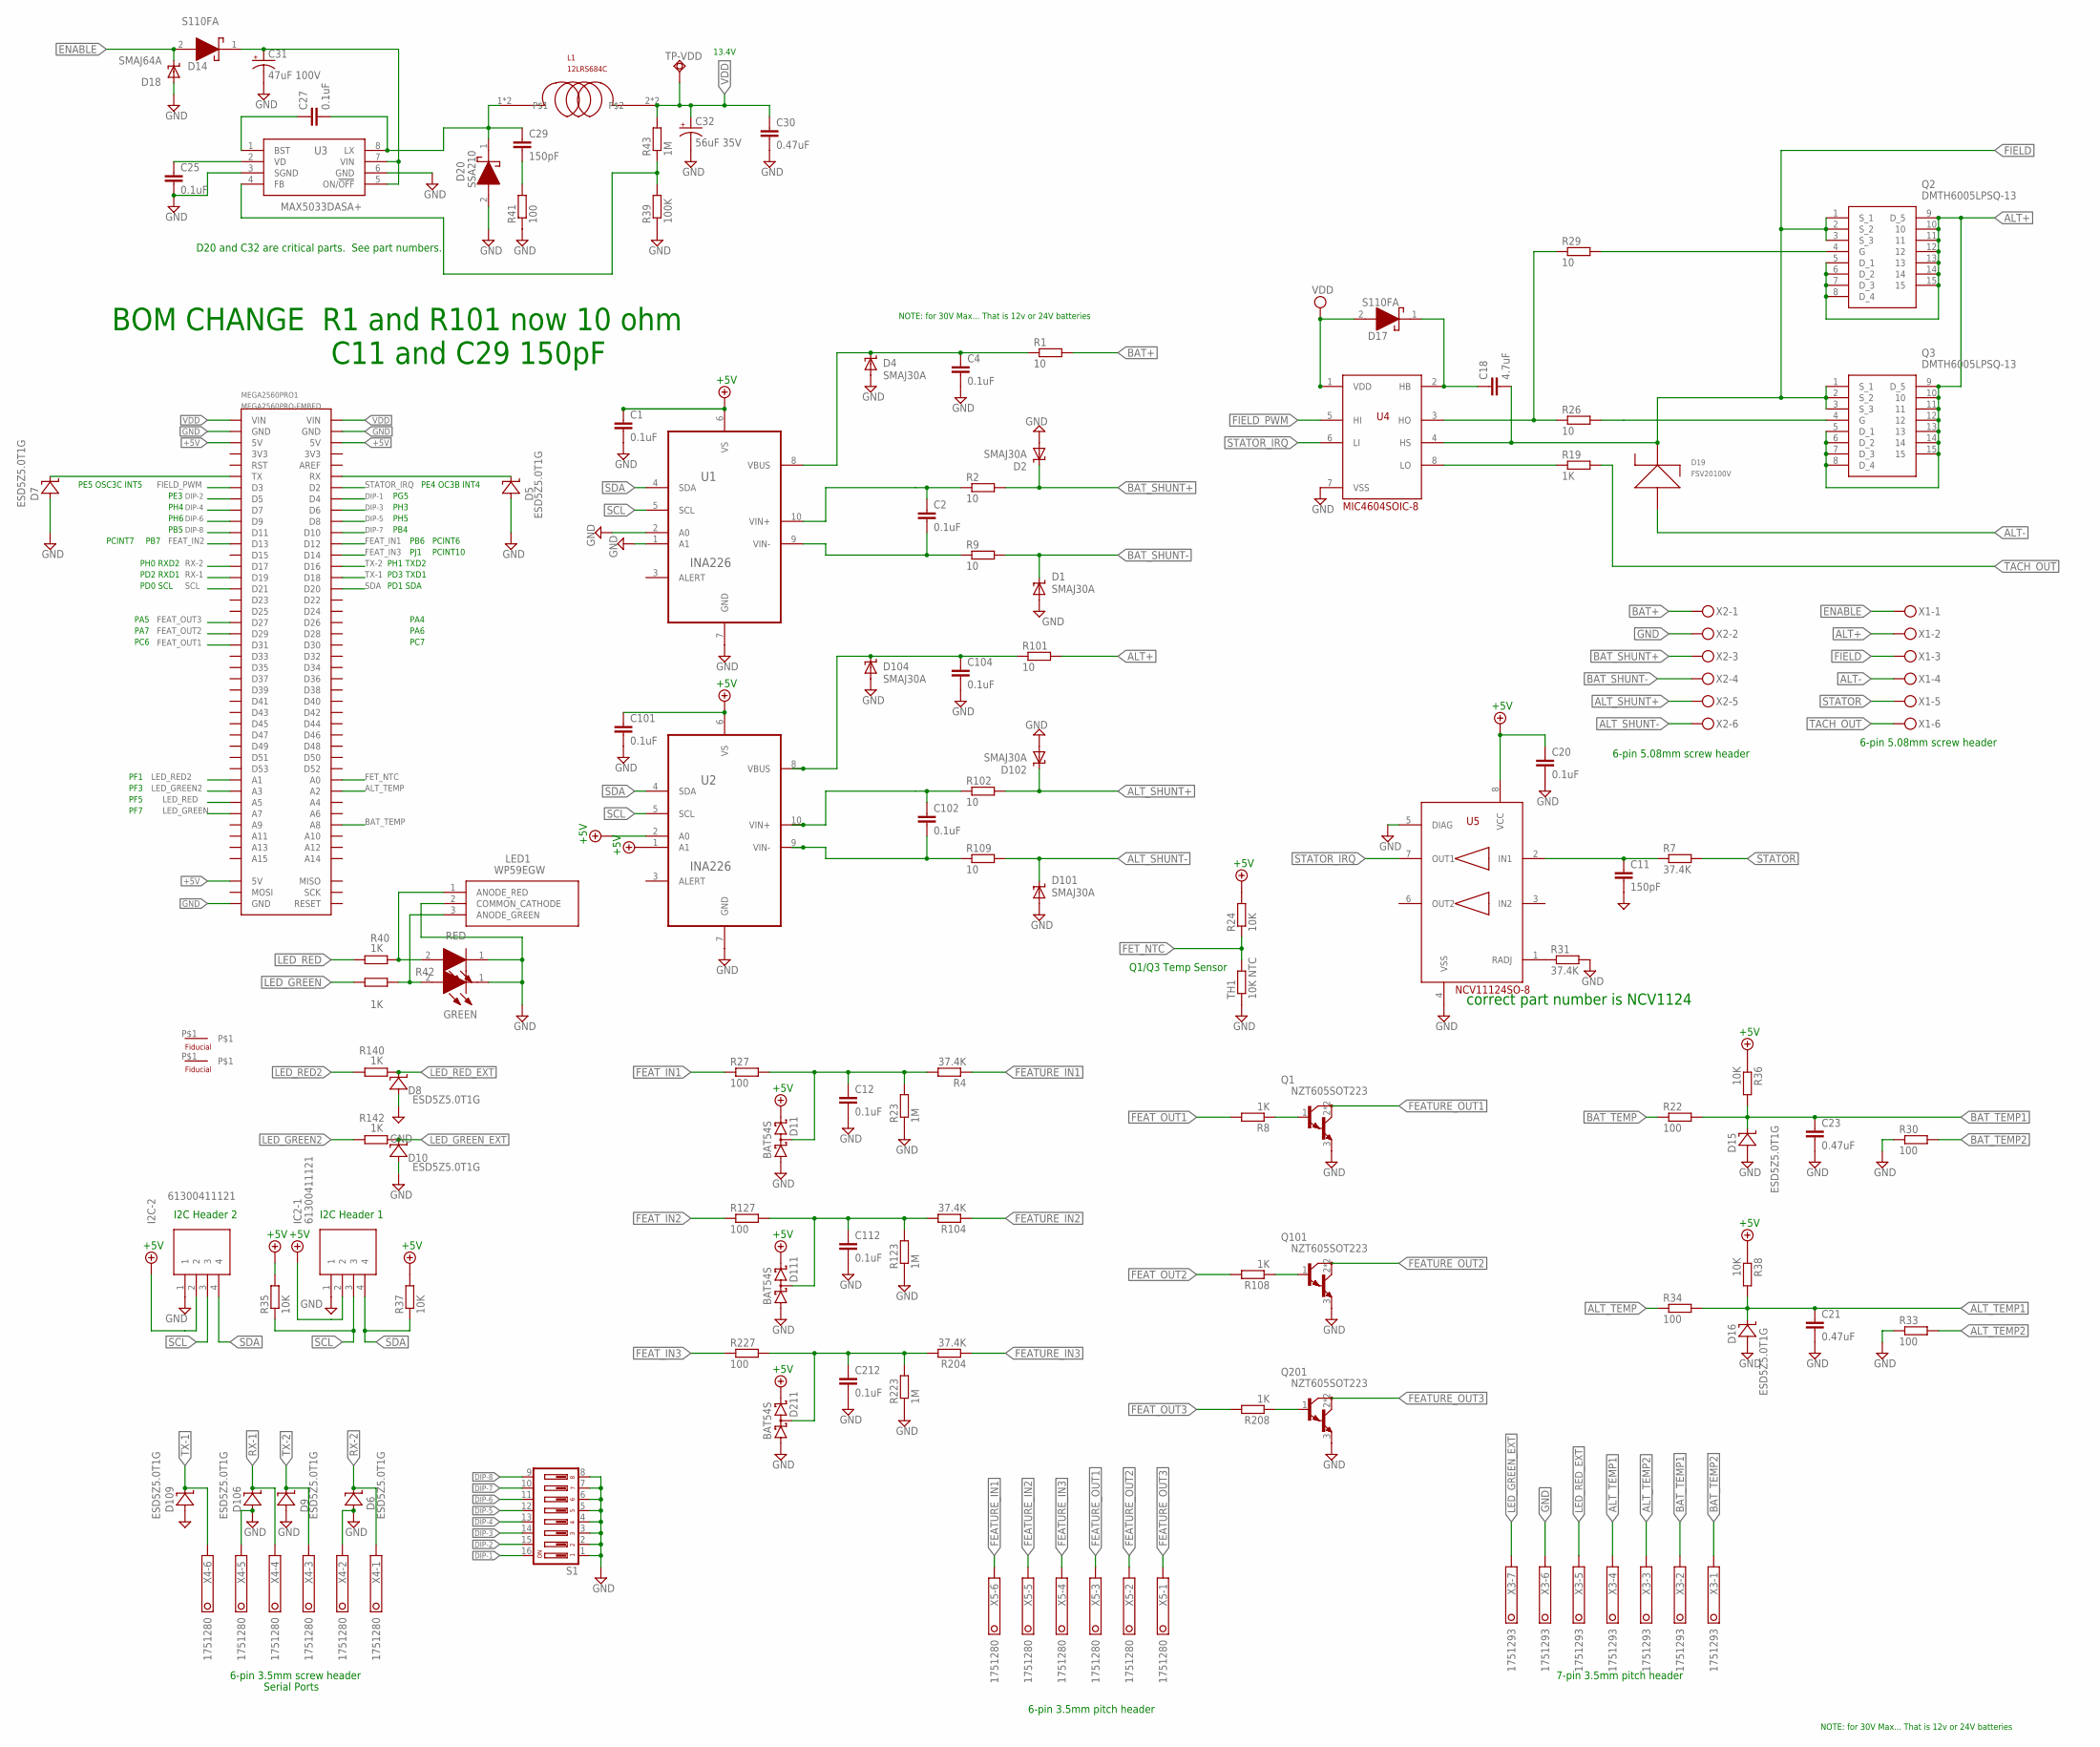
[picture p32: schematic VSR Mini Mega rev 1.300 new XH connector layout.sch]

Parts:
C1, C2, C4, C12, C20, C25, C27, C101, C102, C104, C112, C212: 0.1uF; C0603
C11, C29: 150pF; C0603
C18: 4.7uF; C0603K
C21, C23, C30: 0.47uF; C0603
C31: 47uF 100V; CAPPRD500W60D1000H1250B
C32: 56uF 35V; CAPPRD250W50D630H1100B
D1, D2, D4, D101, D102, D104: SMAJ30A; SMBJ
D5, D6, D7, D8, D9, D10, D15, D16, D106, D109: ESD5Z5.0T1G; SOD523
D11, D111, D211: BAT54S; SOT23
D14, D17: S110FA; SODFL3618X143N
D18: SMAJ64A; SMBJ
D19: FSV20100V; TO-277
D20: SSA210; DIOM5227X270N
FIDUCIAL1, FIDUCIAL2: FIDUCIAL060
GREEN: 599-0110-007F; LEDM2012X90N
I2C-2: 61300411121; HDRV4W95P0X254_1X4_1016X254X85
IC2-1: 61300411121; HDRV4W95P0X254_1X4_1016X254X85
L1: 12LRS684C; IND_12LRS156C
LED1: WP59EGW; T-1_3/4(5MM)_BI-COLOR_INDICATO
MEGA2560PRO1: MEGA2560PRO-EMBED
Q1, Q101, Q201: NZT605SOT223; SOT223
Q2, Q3: DMTH6005LPSQ-13; DMTH6005LPSQ13
R1, R2, R9, R26, R29, R101, R102, R109: 10; R0603
R4, R7, R31, R104, R204: 37.4K; R0603
R8, R19, R40, R42, R108, R140, R142, R208: 1K; R0603
R22, R27, R30, R33, R34, R41, R127, R227: 100; R0603
R23, R43, R123, R223: 1M; R0603
R24, R35, R36, R37, R38: 10K; R0603
R39: 100K; R0603
RED: 599-0110-007F; LEDM2012X90N
S1: DP08; DP-08
TH1: 10K NTC; R0402
TP-VDD: TPSQTP20SQ; TP20SQ
U1, U2: INA226; SOP50P490X110-10N
U3: MAX5033DASA+; SOIC127P600X175-8N
U4: MIC4604SOIC-8; SOIC8
U5: NCV11124SO-8; SO-8
X1, X2: MKDSN1,5/6-5,08
X3: 1751293
X4, X5: 1751280

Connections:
+5V: C1.1, C20.1, C101.1, D11.2 (C2), D111.2 (C2), D211.2 (C2), I2C-2.2, IC2-1.2, MEGA2560PRO1.5V@1 (5V), MEGA2560PRO1.5V@2 (5V), MEGA2560PRO1.5V@3 (5V), R24.2, R35.2, R36.1, R37.2, R38.1, U1.6 (VS), U2.1 (A1), U2.2 (A0), U2.6 (VS), U5.8 (VCC)
ALT+: Q2.5 (D_1), Q2.6 (D_2), Q2.7 (D_3), Q2.8 (D_4), Q2.9 (D_5), Q2.10, Q2.11, Q2.12, Q2.13, Q2.14, Q2.15, Q3.5 (D_1), Q3.6 (D_2), Q3.7 (D_3), Q3.8 (D_4), Q3.9 (D_5), Q3.10, Q3.11, Q3.12, Q3.13, Q3.14, Q3.15, R101.2, X1.2
ALT-: D19.1, D19.2, X1.4
ALT_SHUNT+: D102.C, R102.2, X2.5
ALT_SHUNT-: D101.C, R109.2, X2.6
ALT_TEMP: MEGA2560PRO1.A2, R34.1
ALT_TEMP1: C21.1, D16.C, R34.2, R38.2, X3.4
ALT_TEMP2: R33.2, X3.3
BAT+: R1.2, X2.1
BAT_SHUNT+: D2.C, R2.2, X2.3
BAT_SHUNT-: D1.C, R9.2, X2.4
BAT_TEMP: MEGA2560PRO1.A8, R22.1
BAT_TEMP1: C23.1, D15.C, R22.2, R36.2, X3.2
BAT_TEMP2: R30.2, X3.1
D111: C112.1, D111.3 (C1A2), R104.2, R123.2, R127.2
DIP-1: MEGA2560PRO1.D4, S1.16
DIP-2: MEGA2560PRO1.D5, S1.15
DIP-3: MEGA2560PRO1.D6, S1.14
DIP-4: MEGA2560PRO1.D7, S1.13
DIP-5: MEGA2560PRO1.D8, S1.12
DIP-6: MEGA2560PRO1.D9, S1.11
DIP-7: MEGA2560PRO1.D10, S1.10
DIP-8: MEGA2560PRO1.D11, S1.9
ENABLE: D14.2 (A), D18.C, X1.1
FEATURE_IN1: R4.1, X5.6
FEATURE_IN2: R104.1, X5.5
FEATURE_IN3: R204.1, X5.4
FEATURE_OUT1: Q1.2 (C), Q1.4 (C), X5.3
FEATURE_OUT2: Q101.2 (C), Q101.4 (C), X5.2
FEATURE_OUT3: Q201.2 (C), Q201.4 (C), X5.1
FEAT_IN1: MEGA2560PRO1.D12, R27.1
FEAT_IN2: MEGA2560PRO1.D13, R127.1
FEAT_IN3: MEGA2560PRO1.D14, R227.1
FEAT_OUT1: MEGA2560PRO1.D31, R8.2
FEAT_OUT2: MEGA2560PRO1.D29, R108.2
FEAT_OUT3: MEGA2560PRO1.D27, R208.2
FET_NTC: MEGA2560PRO1.A0, R24.1, TH1.2
FIELD: C18.2, D19.3, Q2.1 (S_1), Q2.2 (S_2), Q2.3 (S_3), Q3.1 (S_1), Q3.2 (S_2), Q3.3 (S_3), U4.4 (HS), X1.3
FIELD_PWM: MEGA2560PRO1.D3, U4.5 (HI)
GND: C1.2, C4.2, C11.2, C12.2, C20.2, C21.2, C23.2, C25.2, C30.2, C31.2 (-), C32.2 (-), C101.2, C104.2, C112.2, C212.2, D1.A, D2.A, D4.A, D5.A, D6.A, D7.A, D8.A, D9.A, D10.A, D11.1 (A1), D15.A, D16.A, D18.A, D20.2 (A), D101.A, D102.A, D104.A, D106.A, D109.A, D111.1 (A1), D211.1 (A1), GREEN.1 (K), I2C-2.1, IC2-1.1, LED1.2 (COMMON_CATHODE), MEGA2560PRO1.GND@1 (GND), MEGA2560PRO1.GND@2 (GND), MEGA2560PRO1.GND@3 (GND), Q1.3 (E), Q101.3 (E), Q201.3 (E), R23.1, R30.1, R31.2, R33.1, R39.1, R41.1, R123.1, R223.1, RED.1 (K), S1.1, S1.2, S1.3, S1.4, S1.5, S1.6, S1.7, S1.8, TH1.1, U1.1 (A1), U1.2 (A0), U1.7 (GND), U2.7 (GND), U3.3 (SGND), U3.6 (GND), U4.7 (VSS), U5.4 (VSS), U5.5 (DIAG), X2.2, X3.6, X4.2, X4.5
LED_GREEN: MEGA2560PRO1.A7, R42.1
LED_GREEN2: MEGA2560PRO1.A3, R142.1
LED_GREEN_EXT: D10.C, R142.2, X3.7
LED_RED: MEGA2560PRO1.A5, R40.1
LED_RED2: MEGA2560PRO1.A1, R140.1
LED_RED_EXT: D8.C, R140.2, X3.5
unnamed: C102.1, R102.1, U2.10 (VIN+)
unnamed: C102.2, R109.1, U2.9 (VIN-)
unnamed: C2.1, R2.1, U1.10 (VIN+)
unnamed: C2.2, R9.1, U1.9 (VIN-)
unnamed: C104.1, D104.C, R101.1, U2.8 (VBUS)
unnamed: C18.1, D17.1 (K), U4.2 (HB)
unnamed: C12.1, D11.3 (C1A2), R4.2, R23.2, R27.2
unnamed: R26.1, R29.1, U4.3 (HO)
unnamed: C212.1, D211.3 (C1A2), R204.2, R223.2, R227.2
unnamed: Q1.1 (B), R8.1
unnamed: Q2.4 (G), R29.2
unnamed: R19.1, U4.8 (LO)
unnamed: Q3.4 (G), R26.2
unnamed: C11.1, R7.1, U5.2 (IN1)
unnamed: R31.1, U5.1 (RADJ)
unnamed: Q101.1 (B), R108.1
unnamed: C4.1, D4.C, R1.1, U1.8 (VBUS)
unnamed: Q201.1 (B), R208.1
unnamed: C31.1 (+), D14.1 (K), U3.5 (ON/!OFF), U3.7 (VIN)
unnamed: C25.1, U3.2 (VD)
unnamed: C27.1, U3.1 (BST)
unnamed: C27.2, C29.1, D20.1 (K), L1.1, L1.4, U3.8 (LX)
unnamed: D7.C, MEGA2560PRO1.TX
unnamed: C29.2, R41.2
unnamed: LED1.1 (ANODE_RED), R40.2, RED.2 (A)
unnamed: GREEN.2 (A), LED1.3 (ANODE_GREEN), R42.2
unnamed: R39.2, R43.1, U3.4 (FB)
unnamed: D5.C, MEGA2560PRO1.RX
RX-1: D106.C, MEGA2560PRO1.D19, X4.4
RX-2: D6.C, MEGA2560PRO1.D17, X4.1
SCL: I2C-2.3, IC2-1.3, MEGA2560PRO1.D21, R35.1, U1.5 (SCL), U2.5 (SCL)
SDA: I2C-2.4, IC2-1.4, MEGA2560PRO1.D20, R37.1, U1.4 (SDA), U2.4 (SDA)
STATOR: R7.2, X1.5
STATOR_IRQ: MEGA2560PRO1.D2, U4.6 (LI), U5.7 (OUT1)
TACH_OUT: R19.2, X1.6
TX-1: D109.C, MEGA2560PRO1.D18, X4.6
TX-2: D9.C, MEGA2560PRO1.D16, X4.3
VDD: C30.1, C32.1 (+), D17.2 (A), L1.2, L1.3, MEGA2560PRO1.VIN@1 (VIN), MEGA2560PRO1.VIN@2 (VIN), R43.2, TP-VDD.TP, U4.1 (VDD)

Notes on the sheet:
6-pin 3.5mm pitch header
Q1/Q3 Temp Sensor
I2C Header 1
I2C Header 2
6-pin 3.5mm screw header
Serial Ports
6-pin 5.08mm screw header
7-pin 3.5mm pitch header
D20 and C32 are critical parts. See part numbers.
PH0 RXD2
PH1 TXD2
PH5
PH6
PE5 OSC3C INT5
PE4 OC3B INT4
PD3 TXD1
PD2 RXD1
PD1 SDA
PD0 SCL
PB4
PC6
PC7
PB6
13.4V
PF1
PF3
PA5
PA7
PA4
PA6
PE3
PH3
PB5
PH4
NOTE: for 30V Max... That is 12v or 24V batteries
BOM CHANGE R1 and R101 now 10 ohm
PG5
PB7
PJ1
PCINT6

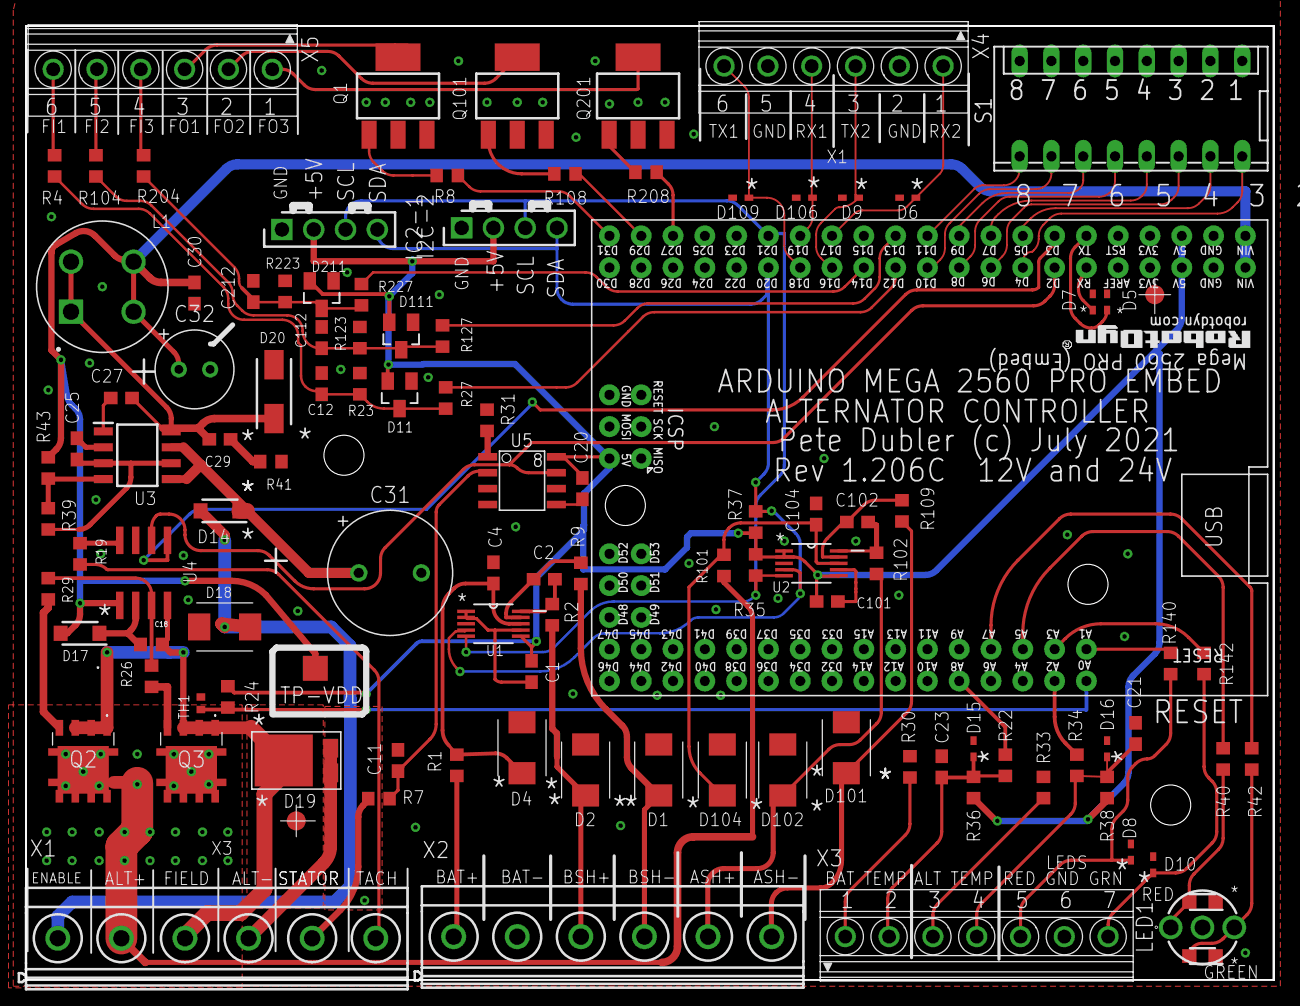
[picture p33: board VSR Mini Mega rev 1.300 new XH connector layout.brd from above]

Board: 2 copper layers, 99.7 x 76.2 mm, 110 parts (0 on the bottom side), 84 nets.

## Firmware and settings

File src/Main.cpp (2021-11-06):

//------------------------------------------------------------------------------------------------------
//
//
//
// Alternator Regulator based on the Arduino IDE
//
//      Copyright (c) 2016, 2017, 2018 by William A. Thomason.      http://arduinoalternatorregulator.blogspot.com/
//
//      Refactored 2020/2021 derivative work (c) 2021 by Pete Dubler
//
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
//
//
//
//
//    This software is a 3/4-stage alternator regulator.  A fundamental difference between this and currently available
//      regulators is the ability to monitor Amps being delivered to the battery as well as Voltage.  By doing so more intelligent
//      charging transitions can be made, resulting in shorter charging times and longer battery life.
//
//      This work is derived from the Smart Engine Control and Alternator Regulator project, and takes the same approach
//      for alternator regulation, but removes all the engine control and integration. http://smartdcgenerator.blogspot.com/
//
//
//    Note special feature, independent of Feature-in selections: 
//        - Shorting NTC sensor the ALTERNATOR will place regulator in 1/2 Alternator amps mode.
//          (Except if Charge Profile #8 LiFePO4 is selected, in that case a HIGH feature-in will cause regulator to stop charging (force to float))
//
//      December 2020 Pete Dubler refactored William A. Thomason's code to remove CAN and Bluetooth related code and move the hardware to a 
//        board with a Mini Mega Pro 2560 daughter card as the processor. "VSR MINI MEGA"
/*
 *      New hardware features include:
 *       - Dual INA226 current voltage sensors (for Alternator and Battery)    
 *       - Three Feature-in Ports and Three Feature-out Ports (functionality and port assignments selectable in Config.h)
 *       - Two serial port screw headers, separate from port used to USB programming, one can support external full function display
 *       - Two I2C pin headers to add OLED display or other features
 */
//
//                ***********************************************
//                * BE SURE TO UPDATE REV_FORK and/or DATE_CODE * 
//                * IN SmartRegulator.h after making changes    *
//                ***********************************************
/*
 *      10/13/20    LIST OF NEW DUBLER FEATURES (Turned on/off with #define statements)
 *                         ENABLE_FEATURE_IN_SCUBA, 
 *                         FEATURE_OUT_GREEN_LED, FEATURE_OUT_RED_LED,
 *                         FEATURE_OUT_LIFEPO_SHUTDOWN_ALARM,
 *                         USE_OLED, USE_SERIAL_DISPLAY ,
 *                         BENCHTEST
 *                          
 *                         
 *                  
*/

#include "Config.h"
#include "SmartRegulator.h"
#include <Wire.h>
#include "Flash.h"
#include "CPE.h"
#include "OSEnergy_Serial.h"
#include "Alternator.h"
#include "System.h"
#include "Sensors.h"
#include "LED.h"
#include "BMS_SERIAL.h"

/***************************************************************************************
****************************************************************************************
*                                                                                      *
                               STARTUP FUNCTIONS
*                                                                                      *
*                                                                                      *
       This is called one time at controller startup.
*                                                                                      *
*                                                                                      *
****************************************************************************************
****************************************************************************************/

//
//------------------------------------------------------------------------------------------------------
// Start-up routine.
//
//      For now both cold start and Watchdog restart will come through here
//
//
//
//------------------------------------------------------------------------------------------------------

void setup()
{

  wdt_enable(WDT_PERIOD); // Because we do SOOO much during setup use the Watchdog during startup...

  Serial.begin(SYSTEM_BAUD); // Start the Serial port.
  while(!Serial){};  // wait for Serial to start successfully

  #ifdef USE_SERIAL_DISPLAY
    if (SERIAL_DISPLAY_PORT != Serial)
    {
      SERIAL_DISPLAY_PORT.begin(SERIAL_DISPLAY_BAUD); // Start the SERIAL_DISPLAY_PORT.
      while(!SERIAL_DISPLAY_PORT){};  // wait for SERIAL_DISPLAY_PORT to start successfully
    }
    // output revision of this code to serial display
    delay(1000); // let remote display boot
    char buffer[40];
    sprintf(buffer, "$D:%d,%s",
         11, // fnCR (which is not in scope here)
         REV_FORK);
    SERIAL_DISPLAY_PORT.println(buffer);
  #endif

  #ifdef USE_BMS_SERIAL_IN
    BMS_SERIAL_PORT.begin(BMS_SERIAL_BAUD); // Start the BMS_SERIAL_PORT.
    while(!BMS_SERIAL_PORT){};  // wait for BMS_SERIAL_PORT to start successfully
  #endif
  
  wdt_reset(); // pat the watchdog timer

  //---  Assign Atmel pins and their functions.
  //         Am using Arduino calls as opposed to Atmel - to make things easier to read.
  //         Make sure to also see the Initialze_xxx(); functions, as they will also assign port values.
  pinMode(LED_RED_PCB, OUTPUT);
  pinMode(LED_GREEN_PCB, OUTPUT);
  pinMode(LED_RED_EXT, OUTPUT);
  pinMode(LED_GREEN_EXT, OUTPUT);

  pinMode(FEATURE_OUT_PORT1, OUTPUT);
  pinMode(FEATURE_OUT_PORT2, OUTPUT);
  pinMode(FEATURE_OUT_PORT3, OUTPUT);

  pinMode(FEATURE_IN_PORT1, INPUT);
  pinMode(FEATURE_IN_PORT2, INPUT);
  pinMode(FEATURE_IN_PORT3, INPUT);

  //----  DIP switch ports.
  pinMode(DIP_BIT0, INPUT_PULLUP); // We will use the weak internal Pull-ups for the DIP switch.
  pinMode(DIP_BIT1, INPUT_PULLUP); 
  pinMode(DIP_BIT2, INPUT_PULLUP);
  pinMode(DIP_BIT3, INPUT_PULLUP);
  pinMode(DIP_BIT4, INPUT_PULLUP);
  pinMode(DIP_BIT5, INPUT_PULLUP); 
  pinMode(DIP_BIT6, INPUT_PULLUP); 
  pinMode(DIP_BIT7, INPUT_PULLUP); 

  wdt_reset(); // pat the watchdog timer

//** good place for TEST CODE

/* 
  for(int i=0;i<8;i++)
  {
    digitalWrite(FEATURE_OUT_PORT1, (i & 1));
    digitalWrite(FEATURE_OUT_PORT2, ((i>>1) & 1));
    digitalWrite(FEATURE_OUT_PORT3, ((i>>2) & 1));
    delay(500);
  }
  
  
  for(;;){};
*/

//**END TEST CODE

  //--------      Adjust System Configuration
  //              Now that things are initialized, we need to adjust the system configuration based on the Users settings of the DIP switches.
  //              We also need to fetch the EEPROM to see if there was a saved 'custom' configuration the user had entered via the GIU.
  //
  //              Note the DIP switches (and hence any selections / adjustments) are sampled ONLY at Power up,
  //
  //------  Read the DIP Switches, and make adjustments to system based on them
  uint8_t dipSwitch;
  dipSwitch = readDipSwitch(); // Read the DIP Switch value

  cpIndex = dipSwitch & 0x07;  //  Mask off the bits indicating the Battery Type - Charge Profile - (CPE) selection
  systemAmpMult = ((float)(((dipSwitch >> 3) & 0x03) + 1)) / 2.0; //  Mask off the bits indicating the Battery Capacity selection and adjust in 250A increments 

  smallAltMode = (dipSwitch >> 5) & 0x01; //  Mask off the bit indicating Small Alternator Capability
 
  tachMode = (dipSwitch >> 6) & 0x01; // Shift and mask off bit for tachMode
  //------  Fetch Configuration files from EEPROM.  The structures already contain their heir 'default' values compiled FLASH.  But we check to see if there are
  //        validated user-saved overrides in EEPROM memory.

  read_SCS_EEPROM(&systemConfig); // See if there are valid structures that have been saved in the EEPROM to overwrite the default (as-compiled) values
  read_CAL_EEPROM(&ADCCal);       // See if there is an existing Calibration structure contained in the EEPROM.

  thresholdPWMvalue = systemConfig.FIELD_TACH_PWM; // Transfer over the users desire into the working variable.  If -1, we will do Auto determine.  If anything else we will just use that
  // value as the MIN PWM drive.  Note if user sets this = 0, they have in effect disabled Tach mode independent DIP switch.
  if (systemConfig.FORCED_TM == true)
    tachMode = true; // If user has set a specific value, or asked for auto-size, then we must assume they want Tach-mode enabled, independent of the DIP

  //---  Initialize library functions and hardware modules
  //
  initialize_sensors();
  initialize_alternator();

  //-----  Sample the System Voltage and adjust system to accommodate different VBats
  //
  delay(100); // It should have only take 17mS for the INA226 to complete a sample, but let's add a bit of padding..
  // Read the voltage to determine the voltage range for the regulator, 12V or 24V
  read_ALT_and_BAT_VoltAmps(); // Sample the voltage the alternator is connected to
   if (measuredAltVolts < 17.0)
    systemVoltMult = 1; //  Likely 12v 'system'
   else
    systemVoltMult = 2; //  must be a 24v 'system'

  //------ Now that we have done all the above work, let's see if the user has chosen to override any of the features!

  if (systemConfig.CP_INDEX_OVERRIDE != 0)
    cpIndex = systemConfig.CP_INDEX_OVERRIDE - 1;
  if (systemConfig.BC_MULT_OVERRIDE != 0.0)
    systemAmpMult = systemConfig.BC_MULT_OVERRIDE;
  if (systemConfig.SV_OVERRIDE != 0.0)
    systemVoltMult = systemConfig.SV_OVERRIDE;
  if (systemConfig.ALT_AMPS_LIMIT != -1)
    altCapAmps = systemConfig.ALT_AMPS_LIMIT; // User has declared alternator size - make sure it is recognized before getting into things.
  // (Needed here in case user has forced regulator to float via feature_in out the door
  //    bypassing RAMP: mode where this variable would normally get checked)

  if (read_CPS_EEPROM(cpIndex, &chargingParms) != true) // See if there is a valid user modified CPE in EEPROM we should be using.
    transfer_default_CPS(cpIndex, &chargingParms);      // No, so prime the working Charge profile tables with default values from the FLASH (PROGMEM) store.

    //---- And after all that, is the user requesting a Master Reset?


#ifdef FEATURE_IN_RESTORE
  if ((digitalRead(FEATURE_IN_RESTORE_PORT) == true) && // Check feature_in port, and do all the 'debounce' when doing so.
        (dipSwitch & MASTER_RESTORE_DIP_CHECK) && //  ONLY do Master Restore if CPE#5  is selected, and all the rest are in defined state.
      (systemConfig.CONFIG_LOCKOUT != 2))
  { //       And the regulator has not been really locked out!
    // feature_in is active, so do a restore all now.
    systemConfig.CONFIG_LOCKOUT = 0; // As this is a HARDWARE restore-all, override any lockout.
    #ifdef USE_OLED
      WriteOLEDFactoryReset();
    #endif
    restore_all();                   // We will not come back from this, as it will reboot after restoring all.
    
  }
#endif


#ifdef USE_OLED 
  WriteOLEDTitlePage();
  WriteOLEDBatteryType();
  wdt_reset(); // pat the watchdog timer
  WriteOLEDDIPSettings();
  WriteOLEDDataScreenStaticData();
#endif
} // End of the Setup() function.

/****************************************************************************************
 ****************************************************************************************
 *                                                                                      *
                                SUPPORTIVE FUNCTIONS
 *                                                                                      *
 *                                                                                      *
        This routines are called from within the Mainloop functions or Startup.
        These are mostly low-level functions to read sensors, keyboards, refresh
           displays, etc...
 *                                                                                      *
 *                                                                                      *
 ****************************************************************************************
 ****************************************************************************************/

//------------------------------------------------------------------------------------------------------
// Stack / Heap stamping
//
//      These functions will place a know pattern (stamp) in un-used memeory between the bottom of the stack
//      and the top of the heap.   Other functions can call later and check to see how much of this
//      'stamping' is retained in order to get an estimate of how much stack space is used during runtime.
//
//      Not quite as good as hardware enforced fences, but better then nothing.
//
//------------------------------------------------------------------------------------------------------
#ifdef DEBUG

void stampFreeStack(void) {
  uint8_t *stmpPtr;
  uint8_t *stkPtr;
  extern unsigned int __heap_start;
  extern void *__brkval;

  if ((int)__brkval == 0)
    stmpPtr = (uint8_t*)&__heap_start;
  else
    stmpPtr = (uint8_t*)__brkval;

  stmpPtr += 8;                                       // Just move a little above the top of the the heap.
  stkPtr  = (unsigned char*) &stkPtr - 8;             // And a little below the current stack pointer.

  //Serial.print("Stamping: ");
  //Serial.print((unsigned int)stmpPtr,HEX);
  //Serial.print(", to: ");
  //Serial.println((unsigned int)stkPtr,HEX);

  while (stmpPtr < stkPtr)
    *stmpPtr++ = 0xA5;

}

int checkStampStack(void) {
  unsigned int unusedCnt;
  uint8_t *stmpPtr;
  uint8_t *stkPtr;
  extern unsigned int __heap_start;
  extern void *__brkval;

  if ((int)__brkval == 0)
    stmpPtr = (uint8_t*)&__heap_start;
  else
    stmpPtr = (uint8_t*)__brkval;

  stmpPtr += 8;                      // Just move a little above the top of the the heap.
  stkPtr  = (unsigned char*) &stkPtr - 8;             // And a little below the current stack pointer.

  //Serial.print("Free memory=");
  //Serial.println(freeMemory());

  //Serial.print("Looking from: 0x");
  //Serial.print((unsigned int)stmpPtr,HEX);
  //Serial.print(", to: 0x");
  //Serial.print((unsigned int)stkPtr,HEX);


  unusedCnt = 0;

  while ((stmpPtr < stkPtr) && (*stmpPtr++ == 0xA5))
    unusedCnt++;

  //Serial.print("      Untouched is now: 0x");
  //Serial.println(unusedCnt,HEX);

  return (unusedCnt);
}
#else
int checkStampStack(void) {
  return (-1);  // Need dummy function when not compiling debug..
}
#endif

//------------------------------------------------------------------------------------------------------
// Read DIP Switch
//      This function is called from Startup and will read the DIP switch.  It will return all 7 usable bits
//      assembled into one returned value.  It is also called during the $SCN: command to make sure the DIP switch
//      is set to all-on before allowing initial updating of the Name and Password.
//
//
// For MiniMega, DIP switch mapping is:
 
  //   Bit 0 = SW1 = Charge Profile 0 - Used to select which entry in chargeParms[] array we should be using.
  //   Bit 1 = SW2 = Charge Profile 1
  //   Bit 2 = SW3 = Charge Profile 2
  //   Bit 3 = SW4 = Battery Capacity 0 - Used to indicate 'size' of battery, to adjust exit amp values
  //   Bit 4 = SW5 = Battery Capacity 1 -  SW4  SW5
  //                                        0    0 =  < 250AmpHr
  //                                        1    0 =  250AH to 500AH 
  //                                        0    1 =  500AH to 750AH
  //                                        1    1 =  >750AH
  //   Bit 5 = SW6 = Small Alt Mode     - Is the Alternator a small capability, and hence the amps should be limited to prevent overheating?
  //   Bit 6 = SW7 = Tachometer Mode    - Turn on to make sure some small level of field PWM is always sent, even during Float and Post-Float modes..
  //   Bit 7 = SW8 = Factory Reset (with FEATURE_IN_RESTORE asserted at startup)
//------------------------------------------------------------------------------------------------------

uint8_t readDipSwitch()
{

  uint8_t dipSwitch;

  dipSwitch = digitalRead(DIP_BIT0);         // Start with the LSB switch,
  dipSwitch |= (digitalRead(DIP_BIT1) << 1); // Then read the DIP switches one switch at a time, ORing them at their appropriate bit location,
  dipSwitch |= (digitalRead(DIP_BIT2) << 2); // This approach allows the DIP switch pins to be randomly assigned instead of on one port.
  dipSwitch |= (digitalRead(DIP_BIT3) << 3);
  dipSwitch |= (digitalRead(DIP_BIT4) << 4);
  dipSwitch |= (digitalRead(DIP_BIT5) << 5);
  dipSwitch |= (digitalRead(DIP_BIT6) << 6);
  dipSwitch |= (digitalRead(DIP_BIT7) << 7);

  return (~dipSwitch); // Invert the returned value, as the DIP switches are really pull-downs.  So, a HIGH means switch is NOT active.
} //read_Dip_Switch

//------------------------------------------------------------------------------------------------------
// Manage System State
//      This function look at the system and decide what changes should occur.
//
//      For the stand-alone alternator, it is much simpler - if the Alternator is not running, and not Faulted, start it up!
//
//
//------------------------------------------------------------------------------------------------------

void manage_system_state()
{

  // --------  Do we need to start the Alternator up?

  if ((chargingState == unknown) || (chargingState == disabled)) // || (chargingState == LIFEPO_FORCED_SHUTDOWN))
  {

    set_ALT_PWM(FIELD_PWM_MIN); // Make sure Field is at starting point.
    set_charging_mode(warm_up); // Prepare for Alternator, let manage_ALT() change state into Ramping
    reset_run_summary();        // Zero out the accumulated AHs counters as we start this new 'charge cycle'
  }
} //manage_system_state

//------------------------------------------------------------------------------------------------------
// Reboot
//
//      This function will disable the Alternator and then forces the Atmel CPU to reboot via a watchdog timeout.
//      It is typically called making a change to the EEPROM information to allow the controller to re-initialize
//
//
//
//------------------------------------------------------------------------------------------------------

void reboot()
{

  set_ALT_PWM(0); // 1st, turn OFF the alternator, All the way OFF as we will no longer be managing it...

  wdt_enable(WDT_PERIOD); // JUST IN CASE:  Make sure the Watchdog is enabled!
  //  (And in any case, let it be the shorter reboot watchdog timeout.

  blink_LED(LED_RESETTING, LED_RATE_FAST, -1, OUT_LAMP_MIRROR_RESETTING); // Show that something different is going on...

  ASCII_write("RST;\r\n");  // tell the USB serial world that we are resetting
  Serial_flush(); // And then make sure the output buffer clears before proceeding with the actual reset.

#ifdef USE_OLED
  WriteOLEDResetting();
#endif

#ifdef USE_SERIAL_DISPLAY // Clear fault display line
  char buffer[40];
  sprintf(buffer, "$D:%d,%s",
          11, // CAUTION hard-coded for fnFL
          "          ");
  SERIAL_DISPLAY_PORT.println(buffer);
#endif
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
void loop()
{
  // first things first, check if BMS is getting ready to shutdown
  #ifdef USE_BMS_SERIAL_IN
    if(checkBMS_Serial_In())
    {
       chargingState = LIFEPO_FORCED_SHUTDOWN;
       //TODO add code for fault state (and new fault code)
    }
  #endif

  if (chargingState == FAULTED)
  {
    wdt_disable();            // Turn off the Watch Dog so we do not 'restart' things.
    handle_fault_condition(); // Take steps to protect system

    if (faultCode & 0x8000U) // If the Restart flag is set in the fault code,
    {
      reboot();              //    then do a forced software restart of the regulator
    }
    //else

    for(;;){} // ain't going nowhere... return; // Else bail out, we will need a full hardware reset from the user.
  }

  //
  //
  //-------   OK, we are NOT in a fault condition.  Let's get to business, read Sensors and calculate how the machine should be behaving
  //
  //

  if (read_sensors() == false) return;    // If there was an error in reading a critical sensor we have FAULTED, restart the loop.
                                          // Treat volts and amps sensed directly by the regulator as the ALTERNATOR values. .                                                               

  calculate_RPMs();        // What speed is the engine spinning?
  calculate_ALT_targets(); // With all that known, update the target charging Volts, Amps, Watts, RPMs...  global variables.

  //
  //
  //-------     Now lets adjust the system.  But first, lets make sure we have not exceeded some threshold and hence faulted.
  //
  //

  if (check_for_faults() == true)
    return; // Check for FAULT conditions
  // If we found one, bail out now and enter holding pattern when we re-enter main loop.

  manage_ALT();          // OK we are not faulted, we have made all our calculations. . . let's set the Alternator Field.
  manage_system_state(); // See if the overall System State needs changing.

  //
  //
  //-------     Tell the world what we are doing, and see if they want us to do something else!
  //
  //
  handle_feature_in();
  check_inbound(); // See if any communication is coming in via the Bluetooth (or DEBUG terminal), or Feature-in port.

  update_run_summary(); // Update the Run Summary variables
  send_outbound(false); // And send the status via serial port - pacing the strings out.
  update_LED();         // Set the blinking pattern and refresh it. (Will also blink the FEATURE_OUT if so configured via #defines
  update_feature_out(); // Handle any other FEATURE_OUT mode (as defined by #defines) other then Blinking.

  wdt_reset(); // Pet the Dog so he does not bit us!

} // loop      // All done this time around.  

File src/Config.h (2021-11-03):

//
//      Config.h
//
//      Copyright (c) 2016, 2017, 2018 by William A. Thomason.      http://arduinoalternatorregulator.blogspot.com/
//
//      Refactored 2020/2021 derivative work (c) 2021 by Pete Dubler
//
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
//


#ifndef _CONFIG_H_
#define _CONFIG_H_

#include "SmartRegulator.h" 
                                                       
/****************************************************************************************
 ****************************************************************************************
 *                                                                                      *
 *                              CUSTOMIZING PARAMETERS                                  *
 *                                                                                      *
 *                                                                                      *
 *      Change the following parameters to meet the exact needs of your installation.   *
 *                                                                                      *
 *      These are general settings which most likely need to be changed to meet your    *
 *         needs.   For more advanced settings, see SmartRegulator.h                    *
 *                                                                                      *
 *      See references at the end of this file for DIP switch settings                  *
 *                                                                                      *
 * **************************************************************************************
 ****************************************************************************************/


//*************************************************************************************************************************************
//*************************************************************************************************************************************
// You can turn off the following features by commenting out the #define statements
// Display Options - both OLED and SERIAL_DISPLAY can be used
#define USE_OLED     // to use the Geekcreit SSD1306 I2C OLED which also requires the SoftWire shell to the I2CMaster library
#define OLED_DISPLAY_DEG_IN_F // display temperatures in Degrees F instead of C (comment out for Deg C)

#define USE_SERIAL_DISPLAY  //output LCD change info on serial line
#define SERIAL_DISPLAY_PORT Serial1
#define SERIAL_DISPLAY_BAUD 9600UL

#define USE_BMS_SERIAL_IN  // Serial input for BMS commands 
#define BMS_SERIAL_PORT Serial2
#define BMS_SERIAL_BAUD 9600UL

//Note: for faster bench testing, turn on BENCHTEST in SmartRegulator.h

//*************************************************************************************************************************************
//*************************************************************************************************************************************

//FEATURE_IN and FEATURE_OUT are configured below
//*********************************************************************************************
//*********      SELECT FEATURE_IN TO USE     SELECT UP TO THREE    ***************************
//*********      **BUT BE SURE TO ASSIGN THEM TO DIFFERENT FEATURE_IN_PORTS**      ************
//*********************************************************************************************
//** INSTRUCTIONS:
//*  To turn on a feature-in functionality, first uncomment the feature 
//*     example: to activate the Equalize feature-in functionality:
//*       //#define FEATURE_IN_EQUALIZE   
//*     would be changed to
//*       #define FEATURE_IN_EQUALIZE
//*  Next assign a feature-in port number by uncommenting the next line and changing the last 
//*   character of that line.
//*     example: to assign FEATURE_IN_EQUALIZE to FEATURE_IN_PORT3: 
//*       #define FEATURE_IN_EQUALIZE_PORT FEATURE_IN_PORT3 
//*     would be changed to
//*       define FEATURE_IN_EQUALIZE_PORT FEATURE_IN_PORT2
//* 
//*   NOTE: The order of the Feature-In features below is important because the last one encountered
//*           and active will set the system behavior.
//*********************************************************************************************

//#define FEATURE_IN_EQUALIZE     // Enable FEATURE_IN port to select EQUALIZE mode while regulator is operating
//#define FEATURE_IN_EQUALIZE_PORT FEATURE_IN_PORT3

#define ENABLE_FEATURE_IN_SCUBA
#define ENABLE_FEATURE_IN_SCUBA_PORT FEATURE_IN_PORT1

#ifdef ENABLE_FEATURE_IN_SCUBA
#define FIELD_PWM_SCUBA 23 //some small percent of maximum value for PWM  23 = 9%   32 = 12%
                           //the equation is value = int((target percentage * 255)/100)S
#endif
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

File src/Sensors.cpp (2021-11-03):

//      Sensors.cpp
//
//      Copyright (c) 2016, 2017 by William A. Thomason.      http://arduinoalternatorregulator.blogspot.com/
//
//      Refactored 2020/2021 derivative work (c) 2021 by Pete Dubler
//
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
//

#include "Config.h"
#include "Sensors.h"
#include "Alternator.h"
#include "Flash.h"
#include <Wire.h>

#include <I2Cx.h> // Newer I2C lib with improved reliability and error checking.
                  // Only use with AVR processors

#ifdef USE_OLED
  #include "I2C_OLED.h"
  char buffer2[20];
#else
  #include <SoftI2CMaster.h> // http://homepage.hispeed.ch/peterfleury/avr-software.html
#endif                     //USE_OLED   // DUBLER 061420 new URL https://github.com/felias-fogg/SoftI2CMaster 
                           // It is too bad there are so many of these with the same name.  Be sure to get the correct one
//----  Public  veriables
float measuredAltVolts = 0; // The regulator takes local measurements, and to start with we ASSUME these sensors are connected to the Alternator.  So, we locally measure
float measuredAltAmps = 0;  // ALTERNATOR voltage and current.
float measuredBatVolts = 0; // However, we need to regulate based on Battery voltage and current.  In stand-along installations, we have to assume that what we measure via
float measuredBatAmps = 0;  // the regulator is what we are to 'regulate' to, so the code will copy over the 'alternator' values into the 'battery' values.
// On the Mini Mega version, we have two INA226 voltage and current sensor chips on the I2C bus, one for the battery and one for the alternator.
// TODO Add config setting to not use the alternator INA226

bool shuntAltAmpsMeasured = false; //  TODO need to sort this out...accommodating multi charge sources w/external coordination where the Amp Shunt is installed on the Alternator, not the Battery.
//  usingEXTAmps is a signal that we are using externally supplied amps.  It is used to help assess when this external value times out.
//  shuntAmpsMeasured is a signal that we have ever been able to measure Amps via the shunt - used to disable amp based decisions in
//  manageAlt() when we are not even able to measure Amps....
int measuredAltWatts = 0;
int measuredFETTemp = -99;  // -99 indicated not present.  Temperature of Field FETs, in degrees C.
int measuredAltTemp = -99;  // -99 indicated not present.  -100 indicates user has shorted the Alt probe and we should run in half-power mode.
//int measuredAlt2Temp = -99; // -99 indicated not present.  Value derived from 2nd NTC port if battery temperature is delivered by an external source via the CAN.
int measuredBatTemp = -99;  // -99 indicates we have not measured this yet, or the sender has failed and we need to use Defaults.
// Battery Temperature typically will be measured by the 2nd NTC, the B-NTC port.  However, if the temperature is provided by an external source
//  (Specifically, via the CAN bus), then the 2nd NTC port will be considered a 2nd alternator sensor for alternator temperature regulation.
bool batTempExternal = false; // Have we received the battery temperature from an external source via the CAN?
// Defaults to false for compatibility with non-CAN enabled regulators.

int measuredFieldAmps = -99; // What is the current being delivered to the field?  -99 indicated we are not able to measure it.
bool updatingBatVAs = false; // Are we in the process of updating the Volts and Amps?  (Meaning, hold off doing anything critical until we get new data..)
bool updatingAltVAs = false; 
//----- Calibration buffer
//      Future releases may allow for calibration of individual boards.  Either by user, or by some external manufacturing process.
//      Would allow for use of lower-cost resistors in all the dividers.  This structure is saved in the FLASH of each device.
//      For now, will simple prime these with default values.
tCAL ADCCal = {false, // locked   == Let user do calibration if they wish to.
               1.0,   // .VBAT_GAIN_ERROR  == Error of VBat ADC + resister dividers
               1.0,   // .AMP_GAIN_ERROR
               0,     // .VBAT_OFFSET
               -522}; // TODO Do we need this???   .AMP_OFFSET == ADC Offset error of shunt circuit measured @ 0A

//****************************************************************************************************************************
//i += 522;                                 // VERY BAD!  Original PCB needed to add in a manual offset to accommodate a hardware design error with regard to
// Default offset is now contained          // how common-mode noise is divided by R22/R24, and causes -14.2A to be displayed when no current
// in this  'default' ADCCal structure      // is present in amp shunt.
// IF YOU DO BUILD OPTION OF NOT INSTALLING INA282 LEVEL SHIFTER, CHANGE DEFAULT TO = 0
//****************************************************************************************************************************

//----  Internal veriables and prototypes
uint32_t sensorsLastSampled; // Used in the main loop to force an sensor (INA226, NTC) sample cycle if alternator isn't running.
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

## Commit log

2021-11-06 separated out remote display
    [LCD Bezel 2.4in clamp-down v2.f3d, LCD Bezel 2.4in clamp-down v8a.stl, LCD Bezel 2.4in snap-in v1.f3d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]
2021-12-26 Add files via upload
    In this version, I changed the pinout on the I2C XH connectors so the pins align with the typical 0.96" I2C OLED display board.
    [VSR Mini Mega rev 1.300 new XH connector layout.brd, VSR Mini Mega rev 1.300 new XH connector layout.sch]
2021-12-26 Add files via upload
    added pdf of schematic

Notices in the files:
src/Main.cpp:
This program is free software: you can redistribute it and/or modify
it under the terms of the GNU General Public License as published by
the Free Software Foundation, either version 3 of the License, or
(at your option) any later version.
